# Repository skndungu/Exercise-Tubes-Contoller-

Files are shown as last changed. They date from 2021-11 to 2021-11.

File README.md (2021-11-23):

# Exercise-Tubes-Contoller
Controller for exercise tubes 

# Exercise Tubes Contoller 3 Speed Levels
exercise_drop_tubes_1

Test codes for solenoids driven via io expander and the arduino

The Code is used to test the PCB board and connections with the solenoids, it put on/off the solenoids at intervals of one sec

PCF8574 GPIO Extender
---
i2c addresses, the table below is used to assign the addresses



Programming
---
- Download the codes from the codes from the ⬇️ on the code section, you will get a folder with the name 📁 `Exercise-Tubes-Contoller--master`
- Extract the content of the zipped file, you will get the firmware codes and another folder with the name 📁 `libs` extract the content from the folder and paste it on your 📂 `documents/Arduino/library/` directory to add the lib used in this case
- Compile and run codes
- Upload to the dev board and test out your codes!

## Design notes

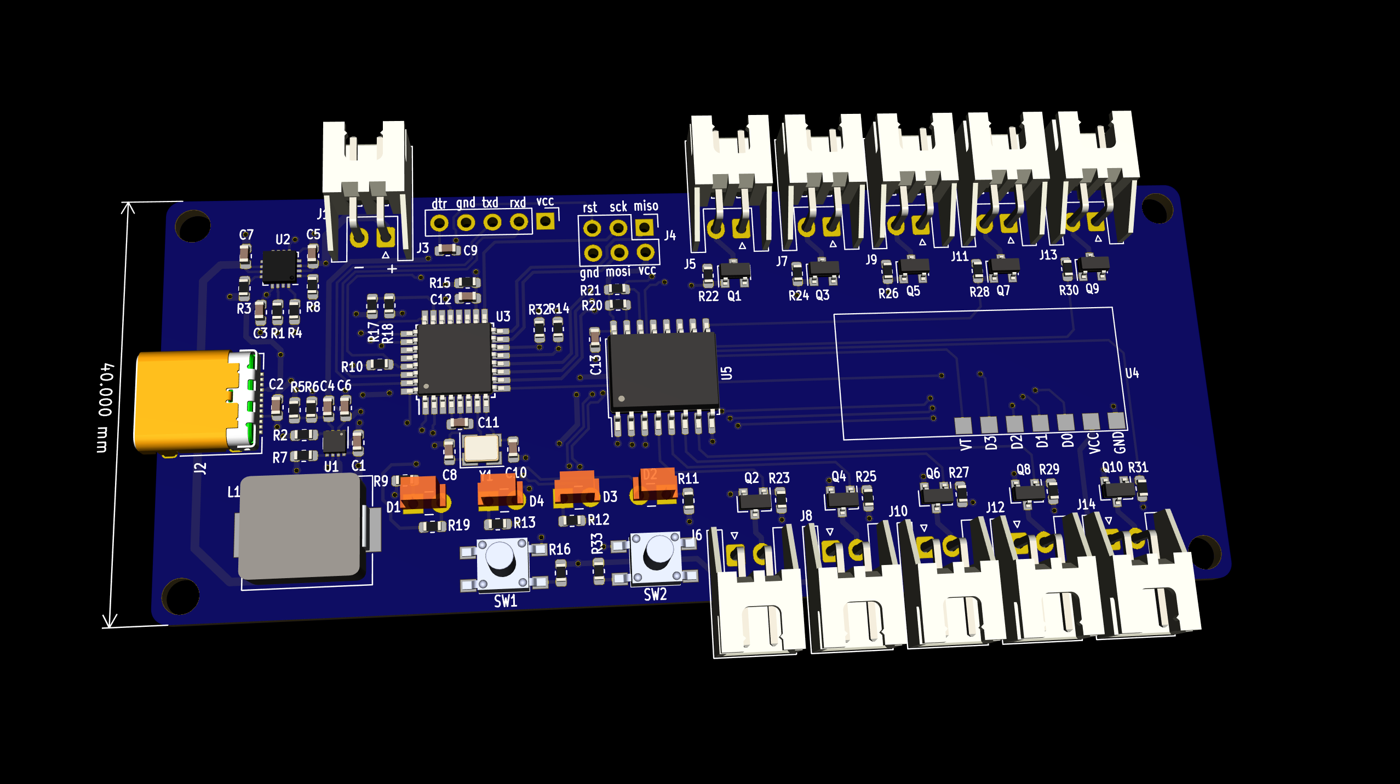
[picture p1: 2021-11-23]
hardware/img/exercise_drop_tubes_1.png

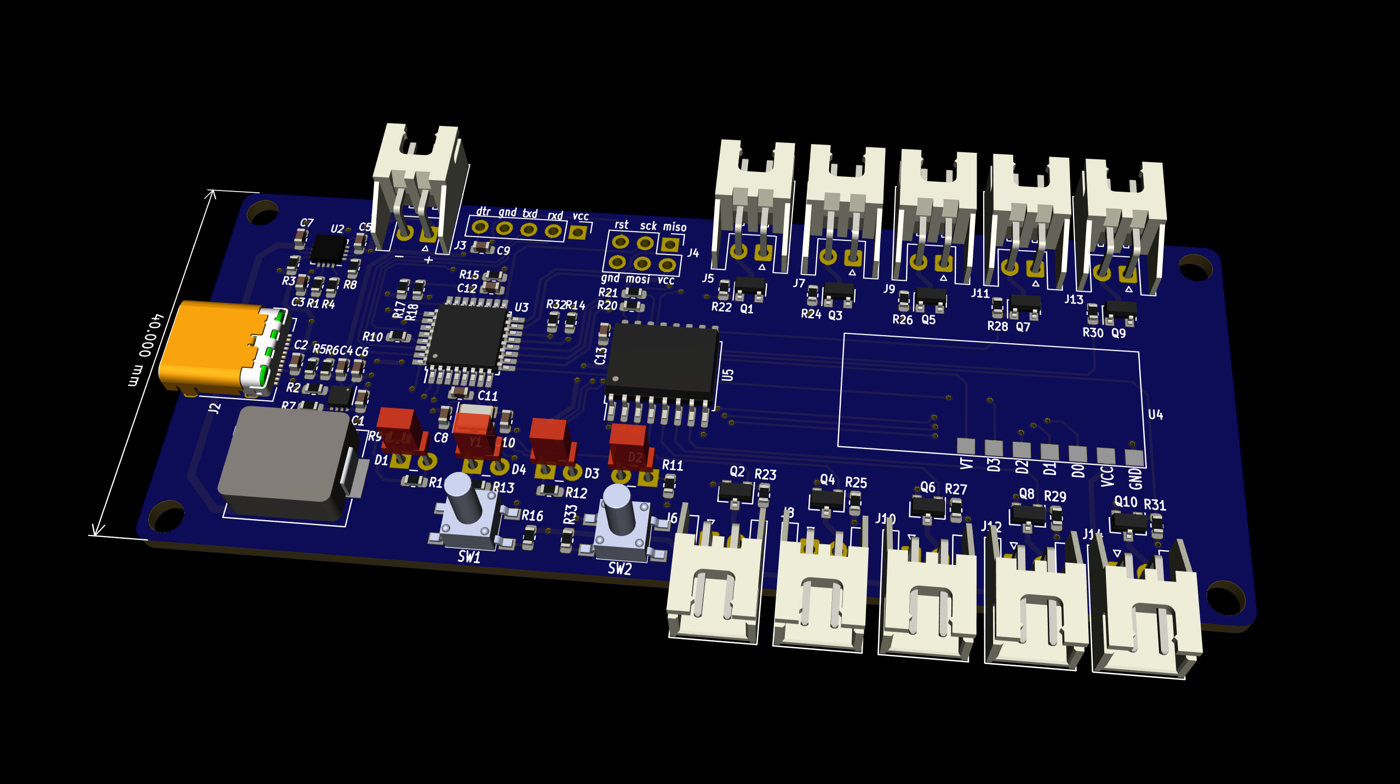
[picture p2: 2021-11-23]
hardware/img/exercise_drop_tubes_2.png

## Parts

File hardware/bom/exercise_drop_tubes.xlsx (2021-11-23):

Reference | Value | Footprint | MFR | Mfr# | VendoR | Vendor part No. | Quantity
C10 C8 | 22p | Capacitor_SMD:C_0603_1608Metric | YAGEO | CC0603JRNPO9BN220 | LCSC |  | 2
C11 C12 C9 C13 | 0.1u | Capacitor_SMD:C_0603_1608Metric | YAGEO | CC0603KRX7R9BB104 | LCSC |  | 4
C3 C7 C5 C2 C1 | 10u | Capacitor_SMD:C_0603_1608Metric | Samsung | CL10A106KP8NNNC | LCSC |  | 5
C4 | 100p | Capacitor_SMD:C_0603_1608Metric | YAGEO | CC0603JRNPO9BN101 | LCSC |  | 1
C6 | 22u | Capacitor_SMD:C_0603_1608Metric | YAGEO | CC0603MRX5R5BB226 | LCSC |  | 1
D1 | Green | LED_THT:LED_Rectangular_W3.0mm_H2.0mm | Kingbright | WP169XGD | MOUSER |  | 1
D3 D4 D2 | LED_Small | LED_THT:LED_Rectangular_W3.0mm_H2.0mm | Kingbright | WP169XID | MOUSER |  | 3
J1 J5 J7 J11 J13 J6 J8 J10 J12 J14 J9 | Conn_01x02 | Connector_JST:JST_XH_S2B-XH-A_1x02_P2.50mm_Horizontal | JST Sales America | S2B-XH-A-1(LF)(SN) | LCSC |  | 11
J2 | USB_C_Receptacle_USB2.0 | Connector_USB:USB_C_Receptacle_Amphenol_12401548E4-2A | Amphenol | 12401548E412A | MOUSER |  | 1
J3 | Conn_01x05 | Connector_PinHeader_2.54mm:PinHeader_1x05_P2.54mm_Vertical |  | A2541WV-5P | LCSC |  | 1
J4 | Conn_02x03_Odd_Even | Connector_PinHeader_2.54mm:PinHeader_2x03_P2.54mm_Vertical |  | PH-00219 | LCSC |  | 1
L1 | 1.5u | greencharge-footprints:YSPI1050-xxx | YJYCOIN | YSPI1050-1R5M | LCSC |  | 1
Q1 Q3 Q5 Q7 Q9 Q2 Q4 Q6 Q8 Q10 | MMBT3904 | Package_TO_SOT_SMD:SOT-23 | PJSEMI | MMBT3904 | LCSC | C411758 | 10
R1 R8 | 50k | Resistor_SMD:R_0603_1608Metric | Viking Tech | AR03BTC5002A | LCSC |  | 2
R10 R18 R21 R20 R14 R32 R22 R24 R26 R28 R30 R23 R25 R27 R29 R31 | 10k | Resistor_SMD:R_0603_1608Metric | YAGEO | RC0603FR-0710KL | LCSC |  | 16
R15 R19 | 0R | Resistor_SMD:R_0603_1608Metric | YAGEO | RC0603FR-070RL | LCSC |  | 2
R17 | 20k | Resistor_SMD:R_0603_1608Metric | YAGEO | RC0603FR-0720KL | LCSC |  | 1
R2 | 6.65k | Resistor_SMD:R_0603_1608Metric | YAGEO | AC0603FR-076K65L | LCSC |  | 1
R3 | 1.07k | Resistor_SMD:R_0603_1608Metric | HKR(Hong Kong Resistors) | RCT031K07FLF | LCSC |  | 1
R4 | 750k | Resistor_SMD:R_0603_1608Metric | YAGEO | RC0603FR-07750KL | LCSC |  | 1
R5 | 715k | Resistor_SMD:R_0603_1608Metric | YAGEO | RC0603FR-07715KL | LCSC |  | 1
R6 | 180k | Resistor_SMD:R_0603_1608Metric | YAGEO | RC0603FR-07180KL | LCSC |  | 1
R7 | 866k | Resistor_SMD:R_0603_1608Metric | YAGEO | AC0603FR-07866KL | LCSC |  | 1
R9 R12 R13 R11 R16 R33 | 1k | Resistor_SMD:R_0603_1608Metric | YAGEO | RC0603FR-071KL | LCSC |  | 6
SW1 SW2 | SW_Push | greencharge-footprints:UK-B0206-G8-160 | USAKRO | UK-B0206-G8-160 | LCSC |  | 2
U1 | TPS61252DSG | Package_SON:WSON-8-1EP_2x2mm_P0.5mm_EP0.9x1.6mm | Texas Instruments | TPS61252DSG | LCSC | C128617 | 1
U2 | BQ24075RGT | Package_DFN_QFN:VQFN-16-1EP_3x3mm_P0.5mm_EP1.68x1.68mm_ThermalVias | Texas Instruments | BQ24075RGTR | LCSC | C15464 | 1
U3 | ATmega328P-A | Package_QFP:TQFP-32_7x7mm_P0.8mm | Microchip | ATMEGA328P-AU | LCSC | C14877 | 1
U4 | 433MHz-RF | greencharge-footprints:RF-RX-433 |  | RX480E-4 | https://www.daraz.pk/products/geekcreit-rx480e-4-433mhz-wireless-rf-receiver-learning-code-decoder-module-4-channel-output-i169374650.html |  | 1
U5 | PCF8574A | Package_SO:SOIC-16W_7.5x10.3mm_P1.27mm | NXP Semicon | PCF8574T/3,518 | LCSC |  | 1
Y1 | 16MHz | Crystal:Crystal_SMD_Abracon_ABM8G-4Pin_3.2x2.5mm | Yangxing Tech | X322516MLB4SI | LCSC |  | 1

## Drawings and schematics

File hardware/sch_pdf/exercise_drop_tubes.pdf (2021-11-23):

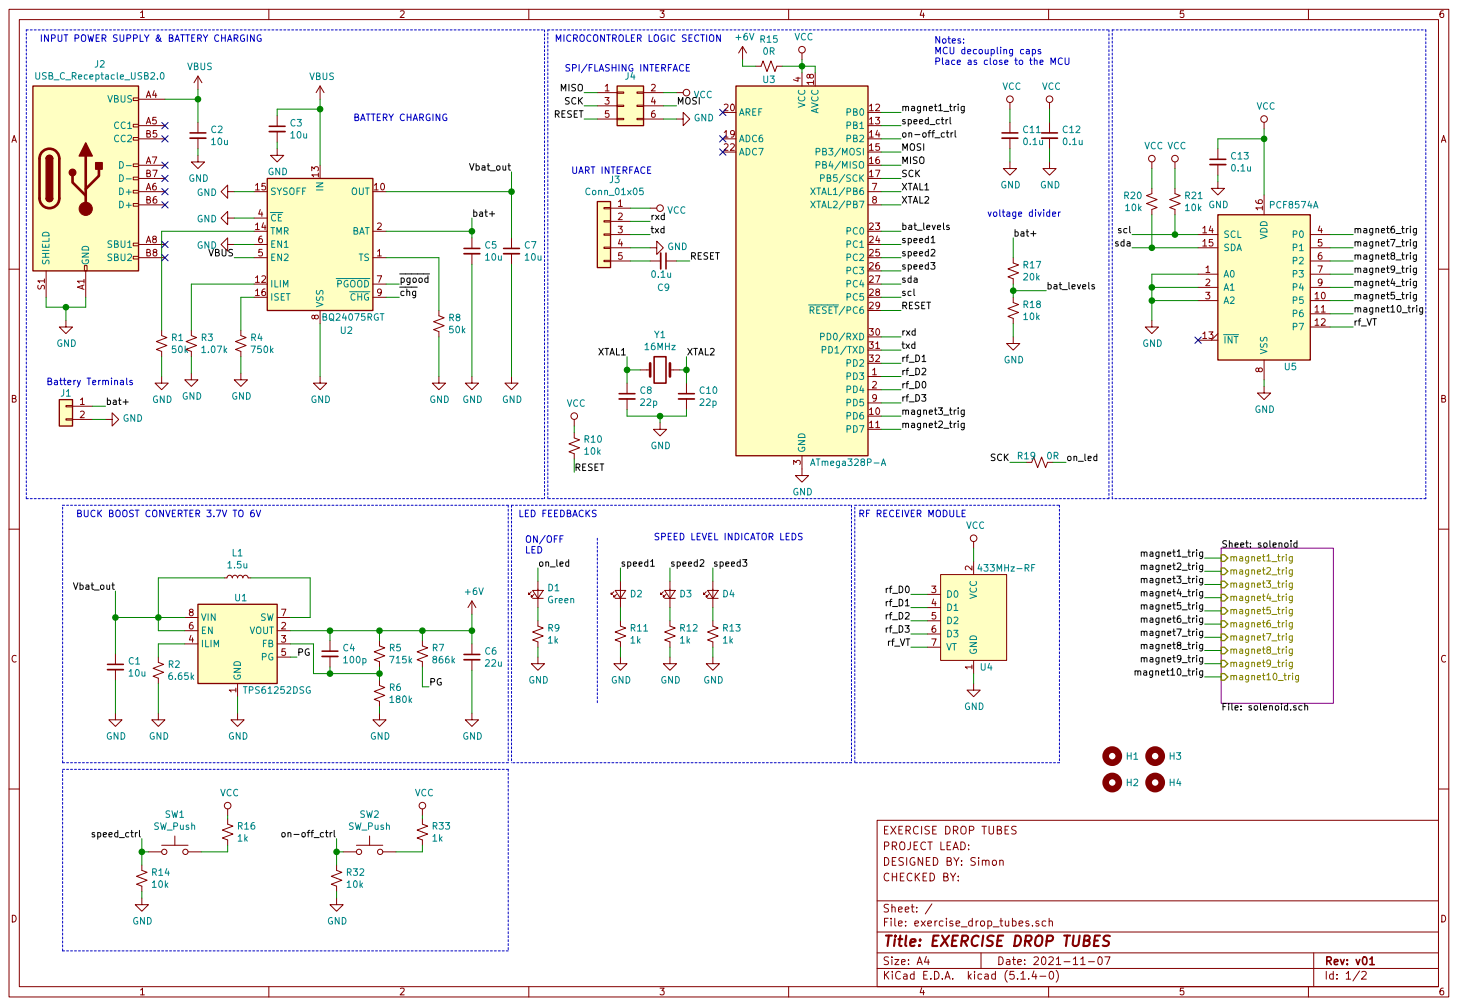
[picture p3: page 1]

INPUT POWER SUPPLY & BATTERY CHARGING

Sheet: solenoid File: solenoid.sch magnet1_trig

File: exercise_drop_tubes.sch Sheet: / CHECKED BY: DESIGNED BY: Simon PROJECT LEAD: EXERCISE DROP TUBES

Id: 1/2 Title: EXERCISE DROP TUBES

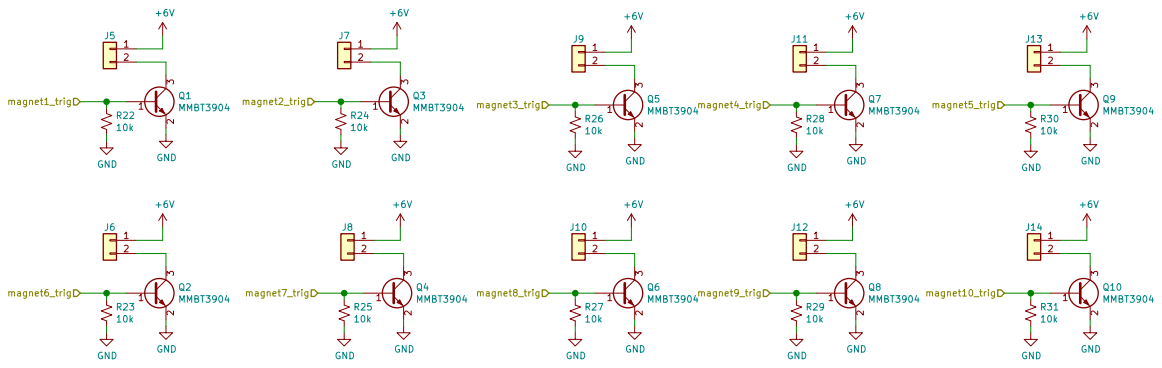
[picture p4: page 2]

File: solenoid.sch Sheet: /solenoid/ CHECKED BY: DESIGNED BY: Simon PROJECT LEAD: EXERCISE DROP TUBES

Id: 2/2 Title: EXERCISE DROP TUBES

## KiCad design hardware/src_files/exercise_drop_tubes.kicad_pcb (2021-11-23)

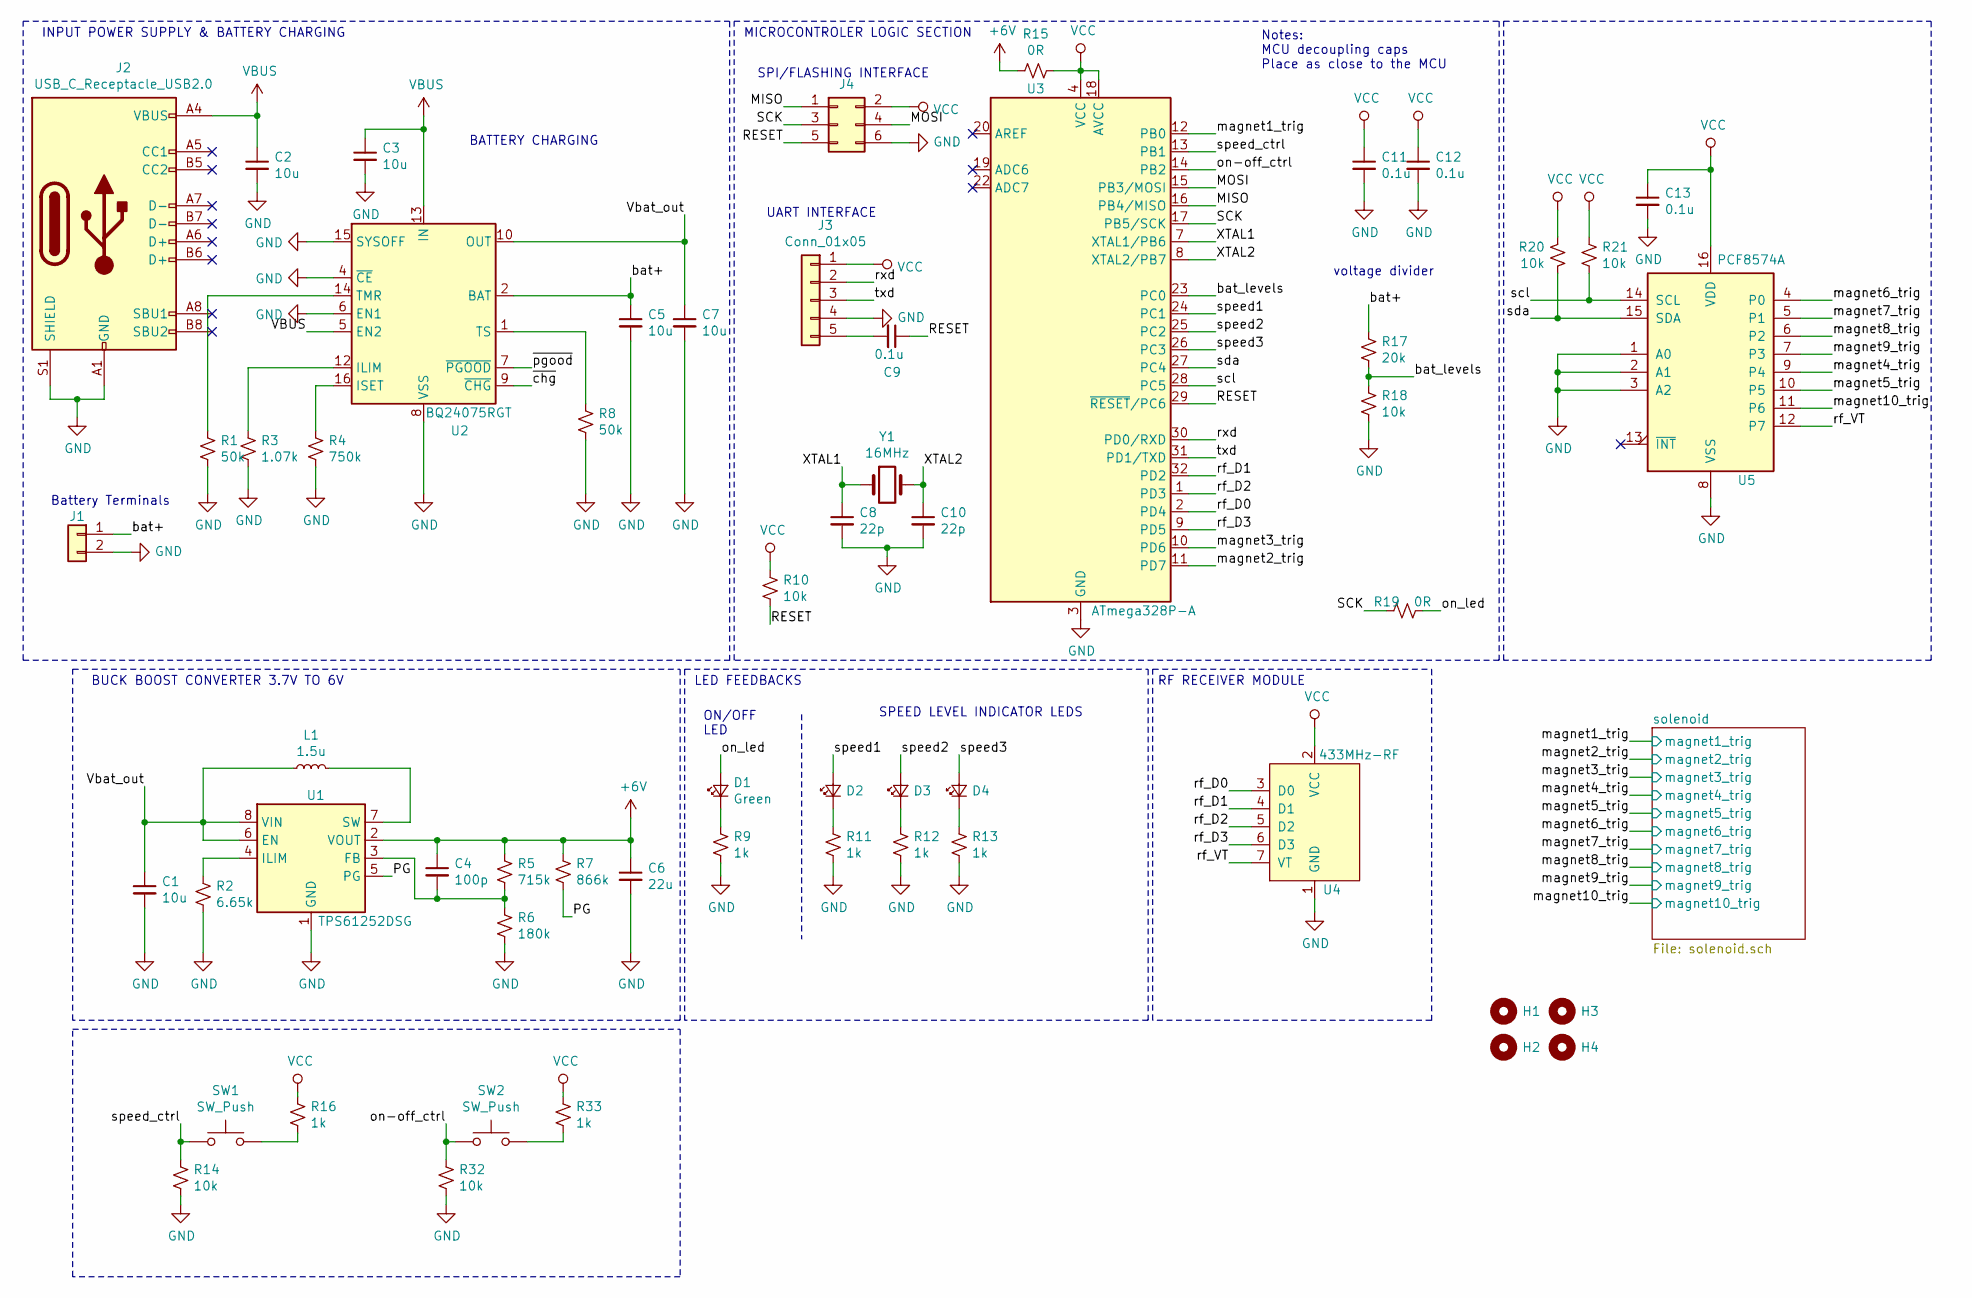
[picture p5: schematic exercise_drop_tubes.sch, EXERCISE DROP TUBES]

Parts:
C1, C2, C3, C5, C7: 10u; C_0603_1608Metric
C4: 100p; C_0603_1608Metric
C6: 22u; C_0603_1608Metric
C8, C10: 22p; C_0603_1608Metric
C9, C11, C12, C13: 0.1u; C_0603_1608Metric
D1: Green; LED_Rectangular_W3.0mm_H2.0mm
D2, D3, D4: LED_Small; LED_Rectangular_W3.0mm_H2.0mm
H1, H2, H3, H4: MountingHole; MountingHole_3.2mm_M3
J1: Conn_01x02; JST_XH_S2B-XH-A_1x02_P2.50mm_Horizontal
J2: USB_C_Receptacle_USB2.0; USB_C_Receptacle_Amphenol_12401548E4-2A
J3: Conn_01x05; PinHeader_1x05_P2.54mm_Vertical
J4: Conn_02x03_Odd_Even; PinHeader_2x03_P2.54mm_Vertical
L1: 1.5u; YSPI1050-xxx
R1, R8: 50k; R_0603_1608Metric
R2: 6.65k; R_0603_1608Metric
R3: 1.07k; R_0603_1608Metric
R4: 750k; R_0603_1608Metric
R5: 715k; R_0603_1608Metric
R6: 180k; R_0603_1608Metric
R7: 866k; R_0603_1608Metric
R9, R11, R12, R13, R16, R33: 1k; R_0603_1608Metric
R10, R14, R18, R20, R21, R32: 10k; R_0603_1608Metric
R15, R19: 0R; R_0603_1608Metric
R17: 20k; R_0603_1608Metric
SW1, SW2: SW_Push; UK-B0206-G8-160
U1: TPS61252DSG; WSON-8-1EP_2x2mm_P0.5mm_EP0.9x1.6mm
U2: BQ24075RGT; VQFN-16-1EP_3x3mm_P0.5mm_EP1.68x1.68mm_ThermalVias
U3: ATmega328P-A; TQFP-32_7x7mm_P0.8mm
U4: 433MHz-RF; RF-RX-433; Mfr# RX480E-4
U5: PCF8574A; SOIC-16W_7.5x10.3mm_P1.27mm
Y1: 16MHz; Crystal_SMD_Abracon_ABM8G-4Pin_3.2x2.5mm

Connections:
+6V: C4.1, C6.1, R5.1, R7.1, R15.2, U1.2 (VOUT); also elsewhere on the board
/MISO: J4.1, U3.16 (PB4/MISO)
/MOSI: J4.4, U3.15 (PB3/MOSI)
/PG: R7.2, U1.5 (PG)
/RESET: C9.1, J4.5, R10.1, U3.29 (~RESET~/PC6)
/SCK: J4.3, R19.2, U3.17 (PB5/SCK)
/Vbat_out: C1.1, C7.1, L1.1, U1.6 (EN), U1.8 (VIN), U2.10 (OUT), U2.11 (OUT)
/XTAL1: C8.1, U3.7 (XTAL1/PB6), Y1.1
/XTAL2: C10.1, U3.8 (XTAL2/PB7), Y1.3
/bat+: C5.1, J1.1, R17.1, U2.2 (BAT), U2.3 (BAT)
/bat_levels: R17.2, R18.1, U3.23 (PC0)
/magnet1_trig: U3.12 (PB0); also elsewhere on the board
/magnet2_trig: U3.11 (PD7); also elsewhere on the board
/magnet3_trig: U3.10 (PD6); also elsewhere on the board
/magnet4_trig: U5.9 (P4); also elsewhere on the board
/magnet5_trig: U5.10 (P5); also elsewhere on the board
/magnet6_trig: U5.4 (P0); also elsewhere on the board
/magnet7_trig: U5.5 (P1); also elsewhere on the board
/magnet8_trig: U5.6 (P2); also elsewhere on the board
/magnet9_trig: U5.7 (P3); also elsewhere on the board
/magnet10_trig: U5.11 (P6); also elsewhere on the board
/on-off_ctrl: R32.1, SW2.1, U3.14 (PB2)
/on_led: D1.2 (A), R19.1
/rf_D0: U3.2 (PD4), U4.3 (D0)
/rf_D1: U3.32 (PD2), U4.4 (D1)
/rf_D2: U3.1 (PD3), U4.5 (D2)
/rf_D3: U3.9 (PD5), U4.6 (D3)
/rf_VT: U4.7 (VT), U5.12 (P7)
/rxd: J3.2, U3.30 (PD0/RXD)
/scl: R21.2, U3.28 (PC5), U5.14 (SCL)
/sda: R20.2, U3.27 (PC4), U5.15 (SDA)
/speed1: D2.2 (A), U3.24 (PC1)
/speed2: D3.2 (A), U3.25 (PC2)
/speed3: D4.2 (A), U3.26 (PC3)
/speed_ctrl: R14.1, SW1.1, U3.13 (PB1)
/txd: J3.3, U3.31 (PD1/TXD)
GND: C1.2, C2.2, C3.2, C5.2, C6.2, C7.2, C8.2, C10.2, C11.2, C12.2, C13.2, J1.2, J2.A1 (GND), J2.A12 (GND), J2.B1 (GND), J2.B12 (GND), J2.S1 (SHIELD), J3.4, J4.6, R1.2, R2.2, R3.2, R4.2, R6.2, R8.2, R9.2, R11.2, R12.2, R13.2, R14.2, R18.2, R32.2, U1.1 (GND), U1.9 (GND), U2.4 (~CE), U2.6 (EN1), U2.8 (VSS), U2.15 (SYSOFF), U2.17 (VSS), U3.3 (GND), U3.5 (GND), U3.21 (GND), U4.1 (GND), U5.1 (A0), U5.2 (A1), U5.3 (A2), U5.8 (VSS); also elsewhere on the board
unnamed: C4.2, R5.2, R6.1, U1.3 (FB)
unnamed: C9.2, J3.5
unnamed: D1.1 (K), R9.1
unnamed: D2.1 (K), R11.1
unnamed: D3.1 (K), R12.1
unnamed: D4.1 (K), R13.1
unnamed: L1.2, U1.7 (SW)
unnamed: R1.1, U2.14 (TMR)
unnamed: R2.1, U1.4 (ILIM)
unnamed: R3.1, U2.12 (ILIM)
unnamed: R4.1, U2.16 (ISET)
unnamed: R8.1, U2.1 (TS)
unnamed: R16.2, SW1.3
unnamed: R33.2, SW2.3
VBUS: C2.1, C3.1, J2.A4 (VBUS), J2.A9 (VBUS), J2.B4 (VBUS), J2.B9 (VBUS), U2.5 (EN2), U2.13 (IN)
VCC: C11.1, C12.1, C13.1, J3.1, J4.2, R10.2, R15.1, R16.1, R20.1, R21.1, R33.1, U3.4 (VCC), U3.6 (VCC), U3.18 (AVCC), U4.2 (VCC), U5.16 (VDD)

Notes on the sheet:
Notes: MCU decoupling caps Place as close to the MCU
Battery Terminals
voltage divider
INPUT POWER SUPPLY & BATTERY CHARGING
BUCK BOOST CONVERTER 3.7V TO 6V
MICROCONTROLER LOGIC SECTION
UART INTERFACE
SPI/FLASHING INTERFACE
BATTERY CHARGING
ON/OFF LED
SPEED LEVEL INDICATOR LEDS
LED FEEDBACKS
RF RECEIVER MODULE

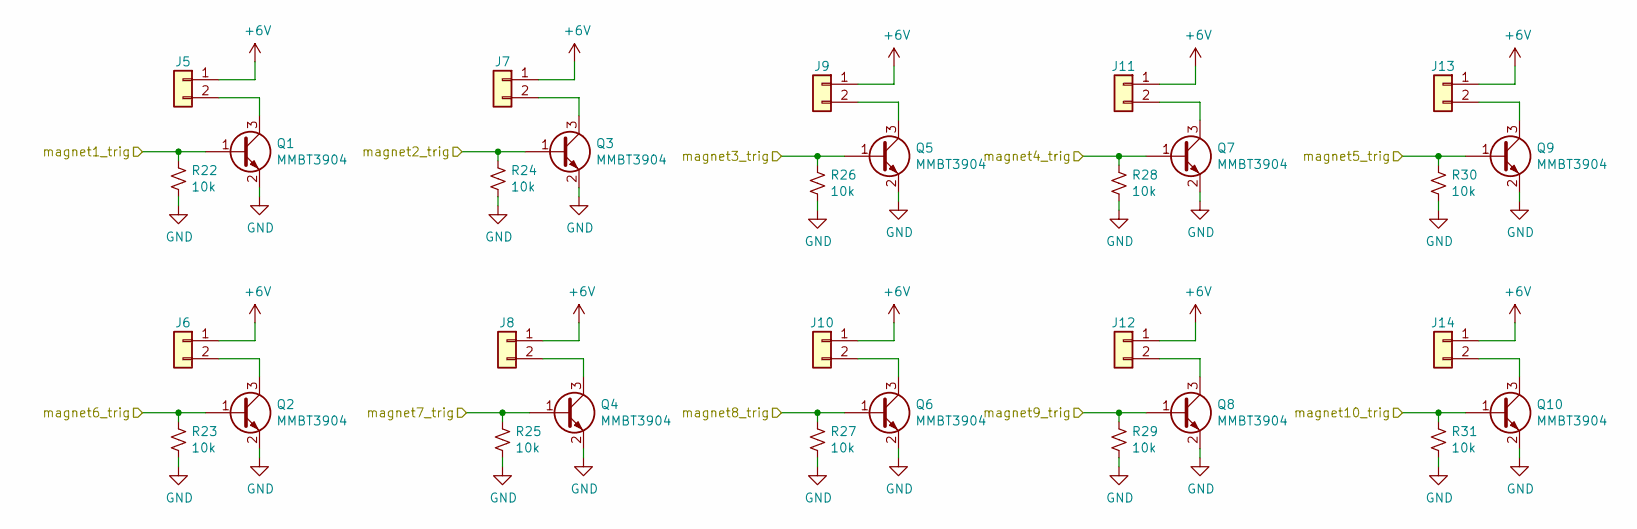
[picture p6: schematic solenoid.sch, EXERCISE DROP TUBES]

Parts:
J5, J6, J7, J8, J9, J10, J11, J12, J13, J14: Conn_01x02; JST_XH_S2B-XH-A_1x02_P2.50mm_Horizontal
Q1, Q2, Q3, Q4, Q5, Q6, Q7, Q8, Q9, Q10: MMBT3904; SOT-23
R22, R23, R24, R25, R26, R27, R28, R29, R30, R31: 10k; R_0603_1608Metric

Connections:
+6V: J5.1, J6.1, J7.1, J8.1, J9.1, J10.1, J11.1, J12.1, J13.1, J14.1; also elsewhere on the board
/magnet1_trig: Q1.1 (B), R22.1; also elsewhere on the board
/magnet2_trig: Q3.1 (B), R24.1; also elsewhere on the board
/magnet3_trig: Q5.1 (B), R26.1; also elsewhere on the board
/magnet4_trig: Q7.1 (B), R28.1; also elsewhere on the board
/magnet5_trig: Q9.1 (B), R30.1; also elsewhere on the board
/magnet6_trig: Q2.1 (B), R23.1; also elsewhere on the board
/magnet7_trig: Q4.1 (B), R25.1; also elsewhere on the board
/magnet8_trig: Q6.1 (B), R27.1; also elsewhere on the board
/magnet9_trig: Q8.1 (B), R29.1; also elsewhere on the board
/magnet10_trig: Q10.1 (B), R31.1; also elsewhere on the board
GND: Q1.2 (E), Q2.2 (E), Q3.2 (E), Q4.2 (E), Q5.2 (E), Q6.2 (E), Q7.2 (E), Q8.2 (E), Q9.2 (E), Q10.2 (E), R22.2, R23.2, R24.2, R25.2, R26.2, R27.2, R28.2, R29.2, R30.2, R31.2; also elsewhere on the board
unnamed: J5.2, Q1.3 (C)
unnamed: J6.2, Q2.3 (C)
unnamed: J7.2, Q3.3 (C)
unnamed: J8.2, Q4.3 (C)
unnamed: J9.2, Q5.3 (C)
unnamed: J10.2, Q6.3 (C)
unnamed: J11.2, Q7.3 (C)
unnamed: J12.2, Q8.3 (C)
unnamed: J13.2, Q9.3 (C)
unnamed: J14.2, Q10.3 (C)

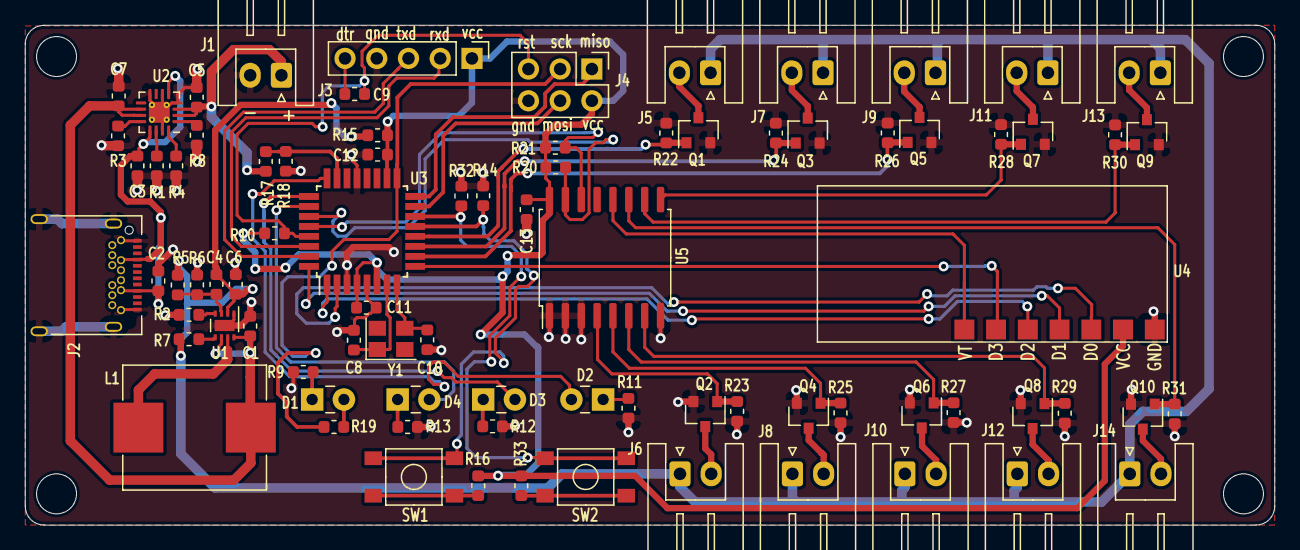
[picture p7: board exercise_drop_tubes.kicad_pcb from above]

Board: 2 copper layers, 100.0 x 40.0 mm, 87 parts (0 on the bottom side), 63 nets.

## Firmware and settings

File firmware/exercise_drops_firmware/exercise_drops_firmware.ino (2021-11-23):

/*
* Title: Exercise Drop Tubes 
*
* Author: Simon Ndungu
*
* Date: 21st Nov 2021
*/
#include "Arduino.h"
#include "PCF8574.h"

/* U5 --> A0,A1,A2 = 0 => address => 0x20 */
/* Set i2c address */ 
// create an object of the PCF8574 
PCF8574 pcf8574_U1(0x20);

#define solenoid1_trig 8
#define solenoid2_trig 7
#define solenoid3_trig 6

#define speed_ctrl_btn 9
#define on_off_ctrl_btn 10

#define bat_level A0

#define speed1_led A1
#define speed2_led A2
#define speed3_led A3
#define status_led 13

#define rf_d0 2
#define rf_d1 3
#define rf_d2 4
#define rf_d3 5

float R1 = 20000;
float R2 = 10000;
float voltage_raw_val = 0.00;
float voltage_out = 0.00;
float battery_voltage = 0.00;
float correction_factor = 0.13;

int random_tube;
int previous_random_tube;
int speed_ctrl_btn_state = 0;
int on_off_ctrl_btn_state = 0;


unsigned long currentMillis=0;
unsigned long previousMillis = 0;
int speed1 = 1000; // value can be changed by buttons
int speed2 = 2000;
int speed3 = 3000; 
int interval; 

bool level1_speed = true;
bool level2_speed = false;
bool level3_speed = false;

int count = 0;



void setup() {
  // put your setup code here, to run once:
	  pcf8574_U1.pinMode(P0, OUTPUT); // solenoid 6
      pcf8574_U1.pinMode(P1, OUTPUT); // solenoid 7
      pcf8574_U1.pinMode(P2, OUTPUT); // solenoid 8
      pcf8574_U1.pinMode(P3, OUTPUT); // solenoid 4
      pcf8574_U1.pinMode(P5, OUTPUT); // solenoid 5
      pcf8574_U1.pinMode(P6, OUTPUT); // solenoid 10
      pcf8574_U1.pinMode(P7, OUTPUT); // RF VT signal

      pinMode(solenoid1_trig, OUTPUT);
      pinMode(solenoid2_trig, OUTPUT);
      pinMode(solenoid3_trig, OUTPUT);

      pinMode(speed1_led, OUTPUT);
      pinMode(speed2_led, OUTPUT);
      pinMode(speed3_led, OUTPUT);
      pinMode(status_led, OUTPUT);

      pinMode(speed_ctrl_btn, INPUT);
      pinMode(on_off_ctrl_btn, INPUT);
      pinMode(bat_level, INPUT);

}

void loop() {
  // put your main code here, to run repeatedly:
   unsigned long currentMillis = millis();

   execute_speed_change();
   
   generate_random_tube(); // executes the tubes

}

void take_reading(){
  voltage_raw_val = analogRead(bat_level);
  speed_ctrl_btn_state = digitalRead(speed_ctrl_btn);
  on_off_ctrl_btn_state = digitalRead(on_off_ctrl_btn);

  Serial.print("Raw Value");
  Serial.println(voltage_raw_val);
}

void check_battery_voltage(){
  take_reading();
  voltage_out = (voltage_raw_val * 5) / 1024; 
  battery_voltage = voltage_out / (R2/(R1+ R2)) - correction_factor;
  Serial.print("Measured Voltage is: ");
  Serial.print(battery_voltage);
  Serial.println("V");
  }


void speed1_led_on(){
   digitalWrite(speed1_led, HIGH);
}
void speed1_led_off(){
  digitalWrite(speed1_led, LOW);
}
void speed2_led_on(){
  digitalWrite(speed2_led, HIGH);
}
void speed2_led_off(){
  digitalWrite(speed2_led, LOW);
}
void speed3_led_on(){
  digitalWrite(speed3_led, HIGH);
}
void speed3_led_off(){
  digitalWrite(speed3_led, LOW);
}

int generate_random_tube(){
   if ((unsigned long )(currentMillis - previousMillis) >= interval) {
      random_tube = random(11);
      Serial.print("Random Number");
      Serial.println(random_tube);
      previousMillis = currentMillis;
      previous_random_tube = random_tube;
   }

   return random_tube;
   trigger_solenoids();
}

void listen_change_speed(){
   if(speed_ctrl_btn_state == 1){
      count +=1;
   }

   if(count == 1){
   	 level1_speed = true;
     level2_speed = false;
     level3_speed = false;
   }

   if(count == 2){
     level1_speed = false;
     level2_speed = true;
     level3_speed = false;
   }

   if(count == 3){
     level1_speed = false;
     level2_speed = false;
     level3_speed = true;
   }

   if(count > 3){
    count = 1; //resets count to 1 if val > 3(reps speed levels)
   }
   
}

void execute_speed_change(){
  listen_change_speed();
  if(level1_speed){
    speed1_led_on();
    speed2_led_off();
    speed3_led_off();
    interval = speed3; // level 1 is the slowest speed 
  }
    if(level2_speed){
    speed1_led_off();
    speed2_led_on();
    speed3_led_off();
    interval = speed2; // level 2 is the medium speed 
  }
    if(level3_speed){
    speed1_led_off();
    speed2_led_off();
    speed3_led_on();
    interval = speed1; // level 1 is the fastest speed 
  }
}

void trigger_solenoids(){
 int tube = generate_random_tube();
 Serial.print("Random Tube Passed is: ");
 Serial.println(tube);
 if(tube == 1){
   digitalWrite(solenoid1_trig, HIGH);
   digitalWrite(solenoid2_trig, LOW);
   digitalWrite(solenoid3_trig, LOW);
   pcf8574_U1.digitalWrite(P0, LOW);
   pcf8574_U1.digitalWrite(P1, LOW);
   pcf8574_U1.digitalWrite(P2, LOW);
   pcf8574_U1.digitalWrite(P3, LOW);
   pcf8574_U1.digitalWrite(P4, LOW);
   pcf8574_U1.digitalWrite(P5, LOW);
   pcf8574_U1.digitalWrite(P6, LOW);
 }
  if(tube == 2){
   digitalWrite(solenoid1_trig, LOW);
   digitalWrite(solenoid2_trig, HIGH);
   digitalWrite(solenoid3_trig, LOW);
   pcf8574_U1.digitalWrite(P0, LOW);
   pcf8574_U1.digitalWrite(P1, LOW);
   pcf8574_U1.digitalWrite(P2, LOW);
   pcf8574_U1.digitalWrite(P3, LOW);
   pcf8574_U1.digitalWrite(P4, LOW);
   pcf8574_U1.digitalWrite(P5, LOW);
   pcf8574_U1.digitalWrite(P6, LOW);
 }
  if(tube == 3){
   digitalWrite(solenoid1_trig, LOW);
   digitalWrite(solenoid2_trig, LOW);
   digitalWrite(solenoid3_trig, HIGH);
   pcf8574_U1.digitalWrite(P0, LOW);
   pcf8574_U1.digitalWrite(P1, LOW);
   pcf8574_U1.digitalWrite(P2, LOW);
   pcf8574_U1.digitalWrite(P3, LOW);
   pcf8574_U1.digitalWrite(P4, LOW);
   pcf8574_U1.digitalWrite(P5, LOW);
   pcf8574_U1.digitalWrite(P6, LOW);
 }
  if(tube == 4){
   digitalWrite(solenoid1_trig, LOW);
   digitalWrite(solenoid2_trig, LOW);
   digitalWrite(solenoid3_trig, LOW);
   pcf8574_U1.digitalWrite(P0, HIGH);
   pcf8574_U1.digitalWrite(P1, LOW);
   pcf8574_U1.digitalWrite(P2, LOW);
   pcf8574_U1.digitalWrite(P3, LOW);
   pcf8574_U1.digitalWrite(P4, LOW);
   pcf8574_U1.digitalWrite(P5, LOW);
   pcf8574_U1.digitalWrite(P6, LOW);
 }
  if(tube == 5){
   digitalWrite(solenoid1_trig, LOW);
   digitalWrite(solenoid2_trig, LOW);
   digitalWrite(solenoid3_trig, LOW);
   pcf8574_U1.digitalWrite(P0, LOW);
   pcf8574_U1.digitalWrite(P1, HIGH);
   pcf8574_U1.digitalWrite(P2, LOW);
   pcf8574_U1.digitalWrite(P3, LOW);
   pcf8574_U1.digitalWrite(P4, LOW);
   pcf8574_U1.digitalWrite(P5, LOW);
   pcf8574_U1.digitalWrite(P6, LOW);
 }
  if(tube == 6){
   digitalWrite(solenoid1_trig, LOW);
   digitalWrite(solenoid2_trig, LOW);
   digitalWrite(solenoid3_trig, LOW);
   pcf8574_U1.digitalWrite(P0, LOW);
   pcf8574_U1.digitalWrite(P1, LOW);
   pcf8574_U1.digitalWrite(P2, HIGH);
   pcf8574_U1.digitalWrite(P3, LOW);
   pcf8574_U1.digitalWrite(P4, LOW);
   pcf8574_U1.digitalWrite(P5, LOW);
   pcf8574_U1.digitalWrite(P6, LOW);
 }
  if(tube == 7){
   digitalWrite(solenoid1_trig, LOW);
   digitalWrite(solenoid2_trig, LOW);
   digitalWrite(solenoid3_trig, LOW);
   pcf8574_U1.digitalWrite(P0, LOW);
   pcf8574_U1.digitalWrite(P1, LOW);
   pcf8574_U1.digitalWrite(P2, LOW);
   pcf8574_U1.digitalWrite(P3, HIGH);
   pcf8574_U1.digitalWrite(P4, LOW);
   pcf8574_U1.digitalWrite(P5, LOW);
   pcf8574_U1.digitalWrite(P6, LOW);
 }
  if(tube == 8){
   digitalWrite(solenoid1_trig, LOW);
   digitalWrite(solenoid2_trig, LOW);
   digitalWrite(solenoid3_trig, LOW);
   pcf8574_U1.digitalWrite(P0, LOW);
   pcf8574_U1.digitalWrite(P1, LOW);
   pcf8574_U1.digitalWrite(P2, LOW);
   pcf8574_U1.digitalWrite(P3, LOW);
   pcf8574_U1.digitalWrite(P4, HIGH);
   pcf8574_U1.digitalWrite(P5, LOW);
   pcf8574_U1.digitalWrite(P6, LOW);
 }
  if(tube == 9){
   digitalWrite(solenoid1_trig, LOW);
   digitalWrite(solenoid2_trig, LOW);
   digitalWrite(solenoid3_trig, LOW);
   pcf8574_U1.digitalWrite(P0, LOW);
   pcf8574_U1.digitalWrite(P1, LOW);
   pcf8574_U1.digitalWrite(P2, LOW);
   pcf8574_U1.digitalWrite(P3, LOW);
   pcf8574_U1.digitalWrite(P4, LOW);
   pcf8574_U1.digitalWrite(P5, HIGH);
   pcf8574_U1.digitalWrite(P6, LOW);
 }
  if(tube == 10){
   digitalWrite(solenoid1_trig, LOW);
   digitalWrite(solenoid2_trig, LOW);
   digitalWrite(solenoid3_trig, LOW);
   pcf8574_U1.digitalWrite(P0, LOW);
   pcf8574_U1.digitalWrite(P1, LOW);
   pcf8574_U1.digitalWrite(P2, LOW);
   pcf8574_U1.digitalWrite(P3, LOW);
   pcf8574_U1.digitalWrite(P4, LOW);
   pcf8574_U1.digitalWrite(P5, LOW);
   pcf8574_U1.digitalWrite(P6, HIGH);
 }
 
}
